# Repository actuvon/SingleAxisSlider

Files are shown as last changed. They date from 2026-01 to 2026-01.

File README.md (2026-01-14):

# Single Axis Slider Project

A simple single-axis CNC motion system for learning about the process of building a custom CNC machine. 

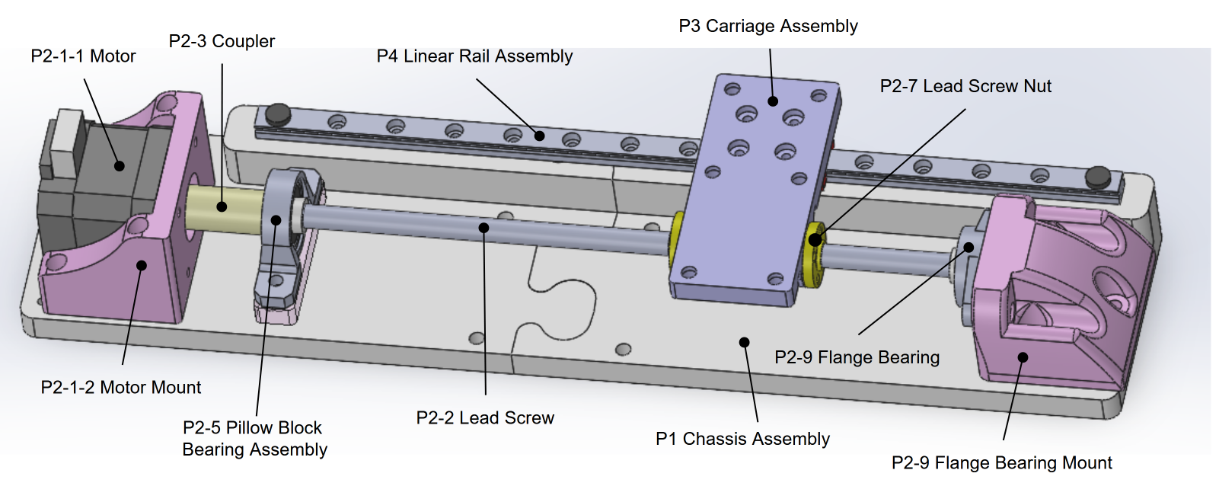
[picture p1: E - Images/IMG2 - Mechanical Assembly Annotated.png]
Mechanical System Diagram D1


## Project objectives (checked when achieved)
- [x] The purpose of this project is to build a cheap motorized linear axis, and to play with different mechanical, electrical, and control options.
- [x] The system should consist of a stepper motor that moves a carriage back and forth along a single axis.
- [x] It should be possible to move the carriage around to specific positions on the axis based on controls from the user.
- [x] A serial/debug interface should be built to let the user try out different settings, or run specific functions on the controller.
- [x] The system should be able to execute standard motion profiles with controlled acceleration and velocity.
- [ ] The controller should be able to run simple g-code programs.
- [ ] The system should include limit switches with auto-homing and collision prevention features.
- [ ] The system should host a web server to lay the groundwork for a user-friendly HMI.
- [ ] The serial/debug interface should be made accessible through the web server via telnet or similar.
- [ ] A web app architecture should be developed to serve an interface to clients which interacts smoothly with the server/controller.
- [ ] A user-friendly HMI should be implemented to jog the motor, home, go to a position, run a g-code command, upload a g-code program, or pause or resume a g-code program that is currently running.
- [ ] The axis should be semi-rigid, so we can pretend that we will use this to mill wood, aluminum, or brass.
- [x] The project should include some basic level of documentation so that readers can get a reasonably good idea of how things work and what's going on.
- [ ] The documentation should be sufficient that someone else could replicate this work, and build the exact same thing.
- [ ] The documentation should be sufficient that a person trying to replicate this work should be able to follow the sequence of decisions that were originally made to build this thing.
- [ ] Use this project as the spindle-carrying X-axis for a full 3-axis CNC mill.

## Files in this repository
Files in this repository are numbered, so that they can be referenced by their document number. Folders in this repository are given letters. Document number 1 in folder C is called document C.1. 
Some folders use part numbers instead of the conventional folder letters. The Part files in folder A and the CAD files in folder B are both examples of this. The CAD folder breaks down it's documents in a slightly different way to keep a clearer revision history.
* **1 - Assembly Definition Document**: This document has the list of parts, and the list of purchase orders and work items that need to be done to build the project. I am working on replacing this Document with MD files such as 3 - Parts.md.
* **3 - Parts.md**: Lists the ID of all parts with a short description and a reference to diagrams that show this part. Includes purchase links and other important details for each part.
* **4 - Ports.md**: TODO: A "Port" is a feature on a part that can be connected to something. It can be a pin/wiring terminal, or it can be a mechanical feature that mates to another mechanical feature on another part. This file details all the ports for each part, which is required to understand document "5 - Connections.md". You often need to look in folder "A - Parts" for a part's "Port Diagram", which shows the name of each port when none is written directly on the part.
* **5 - Connections.md**: TODO: Lists all of the connections between the 'Ports' on various parts. These connections may be made with wires, pipes, fasteners, or others. Notes are given about each connection.
* **6 - TODO.md**: A TODO list to help remind me of the endless pile of tasks yet-to-be-done.
* **Folder A - Parts**: This folder contains detailed information and documents relating to each part. The sub-folders in here are named after the part numbers outlined in document 1 (the assembly definition document). CAD files are not kept in here.
* **Folder B - CAD**: This folder contains all the CAD files, including STL and MDF files used for 3D printing. This is kept seperate from the parts folder to help streamline the CAD modeling workflow. Unfortunately that will make it a bit more of a pain to browse the repository when browsing through parts; you may need to keep one window open for folder A, and another window open for folder B.  Similarly to folder A, all the sub-folders are named after the related part number defined in document 1. I try to keep the STL file for every version of the part that I ever printed, so you can see the progression of changes as I try things and adjust.
* **Folder C - Videos**: As I make YouTube videos to demonstrate different aspects or snapshots of the project, I'll list them here with links and a brief description.
* **Folder D - Diagrams**: All diagrams from document 2 will get exported into here in PDF format. Each diagram will be identified with its diagram number.

## Code
The code that runs on the Arduino Due is kept in the Due's part folder, under **folder A.P5-1.A**. BUT I'll probably move the code over to an entirely different GitHub repo at some point. I'll keep a copy of it here as well though.

I've been uploading this code using PlatformIO, but I think the same code will upload using the Arduino IDE if the main.cpp is renamed to a .ino extension and put in a parent folder with a matching name.

After uploading, I've been accessing the Serial Console using Putty. It should work just fine in the Arduino IDE though. It also works with the PlatformIO terminal.

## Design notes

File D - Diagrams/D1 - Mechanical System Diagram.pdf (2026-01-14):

Rev. 2 - 2026-01-13

A Carriage moves left and right, controlled by a motor that spins a lead screw through a coupler.

The lead screw is supported on one side with a motor, and on the other side with a bearing. The bearing sits on a bearing mount, which bolts to the chassis (shown as ground). On the lead screw rides a carriage assembly. The carriage assembly is driven by two lead screw nuts, which are in turn driven together by the lead screw.

The carriage is supported in linearity and in rotation by the Linear Rail. A Slide is secured to the Linear Rail, and the Carriage is secured to the Slide.

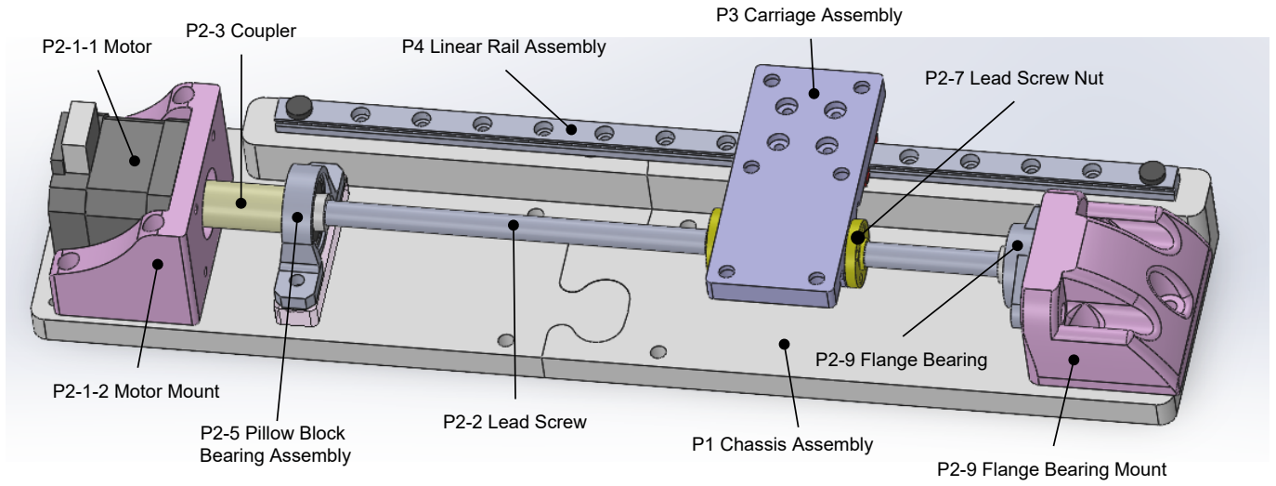
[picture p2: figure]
P1 Chassis Assembly; P2-1-2 Motor Mount; P2-3 Coupler; P2-2 Lead Screw P2-5 Pillow Block; Bearing Assembly; P2-7 Lead Screw Nut; P2-9 Flange Bearing; P2-9 Flange Bearing Mount; P3 Carriage Assembly; P2-1-1 Motor; P4 Linear Rail Assembly

Note: The pillow block bearing was removed from the current version of the assembly because I couldn't get the alignment just right between the linear rail, the flange bearing, the pillow block bearing, and the motor. Failure to align these components perfectly introduces a large amount of friction in the linear rail system. I need to re-develop these parts in a way that makes it possible to align them perfectly.

The ground symbol represents the chassis, which is currently printed in two ABS pieces, joined together. In the future I will want to change this to a single piece of metal, such as a T-rail extrusion.

## D1 - Mechanical System Diagram

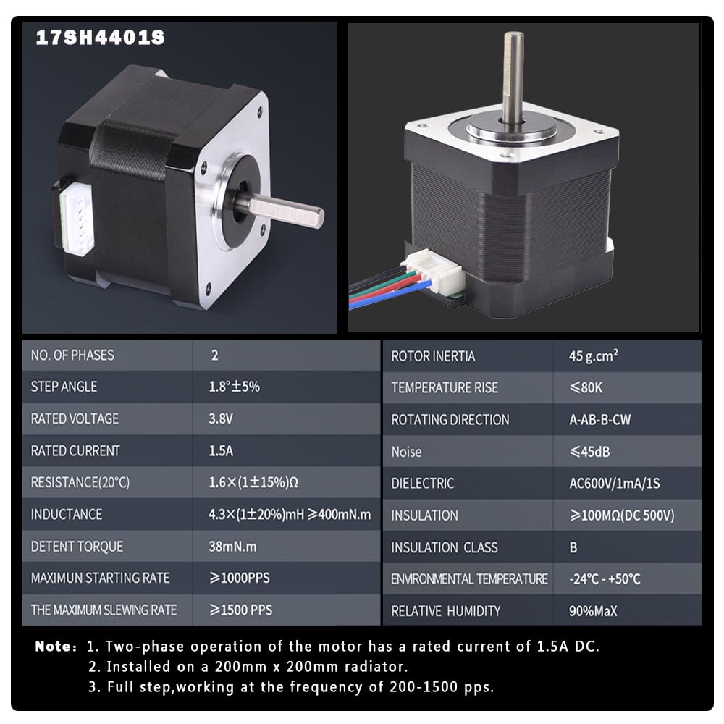
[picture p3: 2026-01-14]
A - Parts/P2-1-1 Stepper Motor/Spec1.jpg

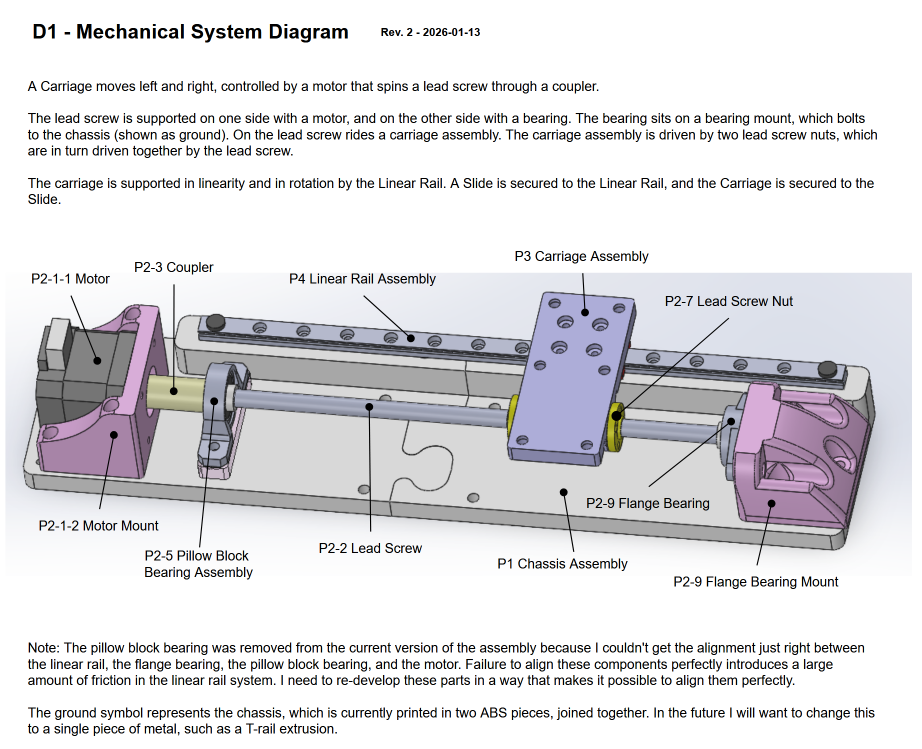
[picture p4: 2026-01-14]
D - Diagrams/D1 - Mechanical System Diagram.png

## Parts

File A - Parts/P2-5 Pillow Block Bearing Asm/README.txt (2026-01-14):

2026-01-13
As of now, this is not in the current version of the build.
The reason is that the alignment wasn't correct enough, so securing this down created too much friction on the lead screw.
When we bring this back, we need to make sure there is enough adjustability to get the alignment perfect.

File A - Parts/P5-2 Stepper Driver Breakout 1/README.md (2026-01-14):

# P5-2 - Stepper Driver Breakout 1

Host board for three DRV8825 stepper driver modules (see part P5-2-2).
Thes boards are capable of microstepping. The breakout board connected the microstep
option pins M0, M1, M2 to !Sleep (called "Wake" here), so the boards are effectively
stuck in 1/32 step mode for maximum microstepping.

Connection numbers start at the red motor power wire and work around counter-clockwise.

Connections
	P5-2:1 	- Motor voltage (red wire). 
			8.2V up to 45V.
			2.5A maximum drive current at 24V and 25°C.

		:2 	- 0V (black wire)
			2.5A maximum drive current.

		:3  - Wake (yellow wire) 

		:4  - Driver 3 !Enable (white wire) (Enable low)
		:5  - Driver 3 Step (blue wire) 
		:6  - Driver 3 Direction (green wire)

		:7	- Driver 2 !Enable (white wire) (Enable low)
		:8  - Driver 2 Step (blue wire)
		:9  - Driver 2 Direction (green wire)

		:10 - Driver 1 !Enable (white wire) (Enable low)
		:11 - Driver 1 Step (blue wire)
		:12 - Driver 1 Direction (green wire)

		:13 - Driver 1 DRIVE B1
		:14 - Driver 1 DRIVE B2
		:15 - Driver 1 DRIVE A1
		:16 - Driver 1 DRIVE A2

		:17 - Driver 2 DRIVE B1
		:18 - Driver 2 DRIVE B2
		:19 - Driver 2 DRIVE A1
		:20 - Driver 2 DRIVE A2

		:21 - Driver 3 DRIVE B1
		:22 - Driver 3 DRIVE B2
		:23 - Driver 3 DRIVE A1
		:24 - Driver 3 DRIVE A2

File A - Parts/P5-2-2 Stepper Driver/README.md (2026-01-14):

#Stepper Driver Breakout 1: Drivers
(parts P-5-2, P-5-3, and P-5-4)

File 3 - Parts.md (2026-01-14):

# Parts

This is a list of all the parts in the system, with brief descriptions.  
To see a **picture/diagram** of the part, check the Diagrams column to see what Diagram(s) it's shown in, then check the related diagram(s) in the **Diagrams folder "D - Diagrams".**  
Details on each part including dimensions, specifications, pinouts, thoughts/plans/problems/rationalle, etc... are given in the **Parts folder "A - Parts".**  
CAD drawings and STL files for 3D Printed parts, or other parts that got modeled for fit are in the **CAD folder "B - CAD".**  
**Purchase links** are provided where possible.  
References to purchase orders (POs), and the PO status are made. These are filled in with MY purchase orders and status; you may wish to clear these columns out and use them for your own build.  
References to Task numbers are made. In the future I want to itemize the tasks needed to perform a build, and create notes/instructions relating to each task.

**Parts in Release #1**

| Part # | Part Name | Part Description | Type | QTY | Connected Parts  | Diagram | PO#  | PO Status | Task # | Task Status | Same as | Purchase Link |
| :--- | :--- | :--- | :--- | :-: | :--- | :--- | :--: | :---: | :----: | :---: | :--- | :---: |
| P1 | Chassis Assembly | The frame that everything else mounts on | Assembly |  1  | P2, P3 | D1 |  x | x | | | | x |
| P1-1 | Chassis Body Print Asm | Both halves of the chassis together | Assembly |  1  | | |  x | x | | | | x |
| P1-1-1 | Chassis Body Print Flange End | The portion of the chassis that the flange bolts to | 3D Print |  1  | | |  x | x | | | | x |
| P1-1-2 | Chassis Body Print Motor End | The portion of the chassis that the motor bolts to | 3D Print |  1  | | |  x | x | | | | x |
| P2 | Drive Assembly | The motor, lead screw, and related supports/power delivery system | Assembly |  1  | | |  x | x | | | | x |
| P2-1 | Motor Assembly | The motor, mount, and related | Assembly |  1  | | D1 |  x | x | | | | x |
| P2-1-1 | Motor | The stepper motor that drives the axis | PO |  1  | P2-1-2 | D1 | PO3  | Received  | x | x | | |
| P2-1-2 | Motor Mount | Mounts the motor to the chassis P1 | 3D Print |  1  | P1, P2-1-1 | D1 |  x | x | | | | |
| P2-1-3 | Motor Mount Screw Asm | Hold the motor to the mount | Assembly |  1  | | |  x | x | | | | x |
| P2-1-3-1 | Motor Mount Screw | | Fastener |  4  | | | | | x | x | | x |
| P2-1-3-2 | Motor Mount Screw Washer | | Fastener |  4  | | | | | x | x | | x |
| P2-2 | Lead Screw | The main transmission element that moves the carriage | PO |  1  | P2-7, P2-7, P2-9 | D1 | PO1  | Received  | x | | | |
| P2-3 | Coupler | Connects the motor shaft to the lead screw | 3D Print |  1  | P2-2 | D1 |  x | x | | | | x |
| P2-7 | Lead Screw Nut | Rides anong the Lead Screw; two are used for anti-backlash adjustment | PO |  2  | | D1 | PO1  | Received  | x | | | |
| P2-9 | Flange Bearing | Holds the end of the Lead Screw opposite the motor | PO |  1  | | D1 | PO8  | Received  | x | | | x |
| P2-10 | Flange Bearing Mount | Holds the flange bearing in place | 3D Print |  1  | | D1 |  x | x | | | | x |
| P3 | Carriage Assembly | | Assembly |  1  | | D1 |  x | x | | | | x |
| P3-1 | Carriage | The main carriage piece | 3D Print |  1  | | |  x | x | | | | x |
| P3-2 | Carriage LeadNut Screws | | Fastener |  8  | | | | | x | | | |
| P3-3 | Carriage LeadNut Screw Nuts | | Fastener |  4  | | | | | x | | | |
| P3-4 | Carriage LeadNut Screw Inserts  | | Fastener |  4  | | | | | x | | | |
| P3-5 | Carriage Slide Screws | | Fastener |  4  | | | | | x | | | |
| P4 | Rail Assembly | | Assembly |  1  | | D1 |  x | x | | | | x |
| P4-1 | Linear Rail | | PO |  1  | | D1 | PO2  | Received  | x | | | |
| P4-2 | Linear Rail Slide | | PO |  1  | | D1 | PO2  | Received  | x | | | |
| P5 | Electronics | | Assembly |  1  | | |  x | x | | | | x |
| P5-1 | Main Controller | Arduino Due | PO |  1  | | | PO10 | Received  | x | | | |
| P5-1-1 | Double-row GPIO Headers Male | | PO |  1  | | | PO5  | Received  | x | | | |
| P5-1-2 | Due Mount | | 3D Print |  1  | | | | | | | | x |
| P5-3 | Independent Stepper Driver 1 | | PO |  1  | | | PO11 | Received  | | | | |
| P5-3-1 | Step Drvr 1 Mount | | 3D Print |  1  | | | | | | | | x |
| P5-3-2 | Step Drvr 1 Mount Clamp | | 3D Print |  2  | | | | | | | | x |
| P5-4 | Control Harness | | Assembly |  1  | | | | | | | | x |
| P5-4-1 | Con: P5-3 Motor side | 8 pin female header | PO |  1  | | | PO12 | Received  | | | | |
| P5-4-2 | Con: P5-3 Ctrl side | 8 pin female header | PO |  1  | | | PO12 | Received  | | | P5-4-1  | |
| P5-4-3 | Due double-row GPIO connector | Dual row female dupont connector | PO |  1  | P5-1-1 | | PO6  | Received  | | | | |
| P5-5 | Brain Mount Plate | Rack plate to host the controller, driver, and connectors | 3D Print |  1  | | | | | | | | x |
| P5-6 | Motor Plug Assembly | | Assembly |  1  | | | | | | | | x |
| P5-6-1 | DB9 Female Connector Asm | | Assembly |  1  | | | | | | | | x |
| P5-6-1-1 | DB9 Female Connector | | PO |  1  | | | | | | | | |
| P5-6-1-2 | DB9 Female Chassis Mount Top | | 3D Print |  1  | | | | | | | | x |
| P5-6-1-3 | DB9 Female Chassis Mount Bottom | | 3D Print |  1  | | | | | | | | x |
| P5-6-1-4 | Female connector mount screws | M5 screws | 3D Print |  2  | | | | | | | | x |
| P5-6-2 | DB9 Male Connector Asm | | Assembly |  1  | | | | | | | | x |
| P5-6-2-1 | DB9 Male Connector | | PO |  1  | | | | | | | | |
| P5-7 | Wires and related | | Misc |  x  | x | x |  x | x | x | x | x | x |
| P5-7-1 | Default hookup wire | 22 AWG stranded silicone-insulated wire kit (multiple colour spools)  | PO | | | | | | | x | | https://www.amazon.ca/dp/B089D29FHC |
| P5-7-2 | Dual DC Power Wire | Dual (Red and Black) 18 AWG silicone-insulated wire spool | PO | | | | | | | x | | https://www.amazon.ca/dp/B07FMRDP87 |
| P5-7-3 | Skinny Hookup Wire | Individual solid-core 28 AWG strands, removed from RJ45 Ethernet wire | PO | | | | | | | x | | https://www.amazon.ca/dp/B0749Y3JTG |
| P6 | Consumables | | Misc |  x  | x | x |  x | x | x | x | x | x |
| P6-1 | ABS Filament | 3D Printer filament used in this project | PO | | | | | | x | x | | |

## Parts not yet added/TODO items

| Part #  | Part Name | Part Description | Type | QTY | Connected Parts | Diagram | PO  | PO Status | Task # | Task Status | Same as | Purchase Link |
| :--- | :--- | :--- | :--- | :-: | :--- | :--- | :-: | :---: | :----: | :---: | :--- | --- |
| P2-11 | Limit Switch A Asm | Not yet implemented | Assembly |  1  | | |  x  | x | | | | |
| P2-11-1 | Limit Switch A | Not yet implemented | PO |  1  | | | PO9 | Planning  | x | | | |
| P2-11-2 | Limit Switch A Mount | Not yet implemented | 3D Print |  1  | | |  x  | x | | | | |
| P2-12 | Limit Switch B Asm | Not yet implemented | Assembly |  1  | | |  x  | x | | | | |
| P2-12-1 | Limit Switch B | Not yet implemented | PO |  1  | | | PO9 | Planning  | x | | | |
| P2-12-2 | Limit Switch B Mount | Not yet implemented | 3D Print |  1  | | |  x  | x | | | | |
| | Rack System | Electronic controls get mounted on plates that get installed in the rack system | Assembly |  1  | | |  x  | x | | | | |

## Inactive/archived parts NOT in above release

| Part # | Part Name | Part Description | Type | QTY | Connected Parts | Diagram | PO  | PO Status | Task # | Task Status | Same as | Purchase Link | Why inactive |
| :--- | :--- | :--- | :--- | :-: | :--- | :--- | :-: | :---: | :----: | :---: | :--- | --- | --- |
| P2-1-4 | Motor Mount Chassis Screw Asm | Hold the mount to the base | Assembly |  4  | | |  x  | x | | | | | Holes don't lign up with chassis |
| P2-1-4-1 | Motor Mount Chassis Screw | | Fastener |  4  | | | | | x | | | | Bad parent really, it's the chassis's fault  |
| P2-1-4-2 | Motor Mount Chassis Screw Nut | | Fastener |  4  | | | | | x | | | | Bad parent really, it's the chassis's fault  |
| P2-3-1 | Coupler Motor Set Screw | | Fastener |  1  | | | | | x | | | | To be added later / Not needed at low torque |
| P2-3-2 | Coupler Leadscrew Set Screw | | Fastener |  1  | | | | | x | | | | To be added later / Not needed at low torque |
| P2-5 | Pillow Block Bearing Assembly | Not in current version - see note in part file | Assembly |  1  | | D1 |  x  | x | | | | | Bad design, causes too much friction |
| P2-5-1 | Pillow Block Bearing | K08 Pillow Block Bearing | PO |  1  | | | PO7 | Received  | x | | | | Bad parent |
| P2-5-2 | Pillow Block Bearing Mount | | 3D Print |  1  | | |  x  | x | | | | | Bad parent |
| P2-5-3 | Pillow Block Mounting Screws  | | Fastener |  2  | | | | | x | | | | Bad parent |
| P5-2 | Stepper Driver Breakout 1 | Perf Board (original design) | Assembly | | | | | | | | | | Replaced with superior part |
| P5-2-1 | SDB1: Perf Board | Board with connections and wires | PO | | | | | | | | | | Bad parent |
| P5-2-2 | SDB1: Driver 1 | Leftmost driver viewed from motor side | PO | | | | | | | | P5-2-1  | | Bad parent |
| P5-2-3 | SDB1: Driver 2 | Middle driver | PO | | | | | | | | P5-2-1  | | Bad parent |
| P5-2-4 | SDB1: Driver 3 | Rightmost driver viewed from motor side | PO | | | | | | | | P5-2-1  | | Bad parent |

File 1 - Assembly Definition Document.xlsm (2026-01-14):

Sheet: Overview
Overview
This document pertains to the single axis slider project. See the README.md.
See document 2 - Single Axis Slider Diagrams
This document relates to build version v0

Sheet: Parts
Systems are made of parts. There are a few main subassemblies in the system.
Each subassembly gets a part number. Some parts of subassemblies come from purchase orders (buying things) and some parts of subassemblies come from work orders (doing things).
Some parts of subassemblies are subassemblies.
In this table we itemise all subassemblies and parts, give them unique numbers, and indicate what diagrams they can be found in and what other parts they connect to.
On the far right, we also link the related purchase orders and work orders, and link in their status so we can monitor our progress as we do a build.
Parts
 |  |  |  |  |  |  |  | Construction Progress
Part # | Part Name | Part Description | Type | Active | QTY | Connected Parts | Diagram | PO | PO Status | Task # | Task Status | Same as
P1 | Chassis Assembly | The frame that everything else mounts on. | Assembly | 1 | 1 | P2, P3 | D1 | x | x
P1-1 | Chassis Body Print Asm | Both halves together | Assembly | 1 | 1 |  |  | x | x
P1-1-1 | Chassis Body Print Flange End |  | 3D Print | 1 | 1 |  |  | x | x
P1-1-2 | Chassis Body Print Motor End |  | 3D Print | 1 | 1 |  |  | x | x
P2 | Drive Assembly |  | Assembly | 1 | 1 |  |  | x | x
P2-1 | Motor Assembly |  | Assembly | 1 | 1 |  |  | x | x
P2-1-1 | Motor | Bipolar stepper motor | PO | 1 | 1 |  |  | PO3 | Received | x | x
P2-1-2 | Motor Mount |  | 3D Print | 1 | 1 |  |  | x | x
P2-1-3 | Motor Mount Screw Asm | Hold the motor to the mount | Assembly | 1 | 1 |  |  | x | x
P2-1-3-1 | Motor Mount Screw |  | Fastener | 1 | 4
P2-1-3-2 | Motor Mount Screw Washer |  | Fastener | 1 | 4
P2-1-4 | Motor Mount Chassis Screw Asm | Hold the mount to the base | Assembly | 1 | 4 |  |  | x | x
P2-1-4-1 | Motor Mount Chassis Screw |  | Fastener | 1 | 4
P2-1-4-2 | Motor Mount Chassis Screw Nut |  | Fastener | 1 | 4
P2-2 | Lead Screw | T8 lead screw | PO | 1 | 1 |  |  | PO1 | Received
P2-3 | Coupler |  | 3D Print | 1 | 1 |  |  | x | x
P2-3-1 | Coupler Motor Set Screw |  | Fastener | 0 | 1
P2-3-2 | Coupler Leadscrew Set Screw |  | Fastener | 0 | 1
P2-5 | Pillow Block Bearing Assembly |  | Assembly | 0 | 1 |  |  | x | x
P2-5-1 | Pillow Block Bearing | K08 Pillow Block Bearing | PO | 0 | 1 |  |  | PO7 | Received
P2-5-2 | Pillow Block Bearing Mount |  | 3D Print | 0 | 1 |  |  | x | x
P2-5-3 | Pillow Block Mounting Screws |  | Fastener | 0 | 2
P2-7 | Lead Screw Nut | T8 lead screw nuts (2 needed) | PO | 1 | 2 |  |  | PO1 | Received
P2-9 | Flange Bearing | K08 Flange bearing | PO | 1 | 1 |  |  | PO8 | Received
P2-10 | Flange Bearing Mount |  | 3D Print | 1 | 1 |  |  | x | x
P2-11 | Limit Switch A Asm |  | Assembly | 1 | 1 |  |  | x | x
P2-11-1 | Limit Switch A |  | PO | 1 | 1 |  |  | PO9 | Planning
P2-11-2 | Limit Switch A Mount |  | 3D Print | 1 | 1 |  |  | x | x
P2-12 | Limit Switch B Asm |  | Assembly | 1 | 1 |  |  | x | x
P2-12-1 | Limit Switch B |  | PO | 1 | 1 |  |  | PO9 | Planning
P2-12-2 | Limit Switch B Mount |  | 3D Print | 1 | 1 |  |  | x | x
P3 | Carriage Assembly |  | Assembly | 1 | 1 |  |  | x | x
P3-1 | Carriage | The main carriage piece | 3D Print | 1 | 1 |  |  | x | x
P3-2 | Carriage LeadNut Screws |  | Fastener | 1 | 8
P3-3 | Carriage LeadNut Screw Nuts |  | Fastener | 1 | 4
P3-4 | Carriage LeadNut Screw Inserts |  | Fastener | 1 | 4
P3-5 | Carriage Slide Screws |  | Fastener | 1 | 4
P4 | Rail Assembly |  | Assembly | 1 | 1 |  |  | x | x
P4-1 | Linear Rail |  | PO | 1 | 1 |  |  | PO2 | Received
P4-2 | Linear Rail Slide |  | PO | 1 | 1 |  |  | PO2 | Received
P5 | Electronics |  | Assembly | 1 | 1 |  |  | x | x
P5-1 | Main Controller | Arduino Due | PO | 1 | 1 |  |  | PO10 | Received
P5-1-1 | Double-row GPIO Headers Male |  | PO | 1 | 1 |  |  | PO5 | Paid
P5-1-2 | Due Mount |  | 3D Print | 1 | 1
P5-2 | Stepper Driver Breakout 1 | Perf Board (original design) | Assembly | 0
P5-2-1 | SDB1: Perf Board | Board with connections and wires |  | 0
P5-2-2 | SDB1: Driver 1 | Leftmost driver viewed from motor side |  | 0
P5-2-3 | SDB1: Driver 2 | Middle driver |  | 0
P5-2-4 | SDB1: Driver 3 | Rightmost driver viewed from motor side |  | 0
P5-2:1 | SDB1: Motor voltage | Red wire |  | 0
P5-2:2 | SDB1: 0V | Black wire |  | 0
P5-2:3 | SDB1: Wake | Yellow wire |  | 0
P5-3 | Independent Stepper Driver 1 |  | PO | 1 | 1 |  |  | PO11 | Received
P5-3-1 | Step Drvr 1 Mount |  | 3D Print | 1 | 1
P5-3-2 | Step Drvr 1 Mount Clamp |  | 3D Print | 1 | 2
P5-4 | Control Harness |  | Assembly | 1 | 1
P5-4-1 | Con: P5-3 Motor side | 8 pin female header | PO | 1 | 1 |  |  | PO12 | Received
P5-4-2 | Con: P5-3 Ctrl side | 8 pin female header | PO | 1 | 1 |  |  | PO12 | Received |  |  | P5-4-1
P5-4-3 | Due double-row GPIO connector | Dual row female dupont connector | PO | 1 | 1 | P5-1-1 |  | PO6 | Paid
P5-5 | Brain Mount Plate | Rack plate to host the controller, driver, and connectors | 3D Print | 1 | 1
P5-6 | Motor Plug Assembly |  | Assembly | 1 | 1
P5-6-1 | DB9 Female Connector Asm |  | Assembly | 1 | 1
P5-6-1-1 | DB9 Female Connector |  | PO | 1 | 1
P5-6-1-2 | DB9 Female Chassis Mount Top |  | 3D Print | 1 | 1
P5-6-1-3 | DB9 Female Chassis Mount Bottom |  | 3D Print | 1 | 1
P5-6-1-4 | Female connector mount screws | M5 screws | 3D Print | 1 | 2
P5-6-2 | DB9 Male Connector Asm |  | Assembly | 1 | 1
P5-6-2-1 | DB9 Male Connector |  | PO | 1 | 1
P6 | Rack System | Electronic controls get mounted on plates that get installed in the rack system | Assembly | 1 | 1

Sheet: POs
This page lists the different purchases that need to be made to build the project. |  |  |  |  |  |  | Statuses:
The line items within each purchase are described in the Order Details sheet. |  |  |  |  |  |  | Planning
Most Order Detail lines should reference parts, but some order lines relate to services instead. |  |  |  |  |  |  | RFQ Submitted
This sheet is about checking what things have or haven't been ordered, and making sure they arrive on time. |  |  |  |  |  |  | Quoted
 |  |  |  |  |  |  | Sent to Accounting
 |  |  |  |  |  |  | Paid
 |  |  |  |  |  |  | Receiving
 |  |  |  |  |  |  | Received
Purchase Orders |  |  | Total : | $364.15 | (CAD)
 |  |  |  |  |  |  |  |  | Purchasing Documents
Order # | Name | Description | Vendor | Amount (CAD) | Included/Cancelled | Status | Last Updated | Last Note | SO# | PO# | QT# | IN#
PO1 | T8 lead screws | QTY 2. The main lead screw for the axis-drive. | Amazon | $54.29 | Included | Received | 2025-11-03 | Order Received
PO2 | Linear Rails | Main linearity provider. | Amazon | $20.14 | Included | Received | 2025-10-31 | Order Received
PO3 | Motors | Two Stepper motors | Amazon | $20.15 | Included | Received | 2025-11-05 | Order Received
PO4 | M3 inserts | 100 inserts | Amazon | $12.31 | Included | Paid | 2025-11-24 | Order placed
PO5 | Due Headers M | Dual row male duponts for the Due | Amazon | $23.40 | Included | Paid | 2025-11-24 | Order placed
PO6 | Due Connectors F | Dual row female duponts for the Due | Amazon | $19.48 | Included | Paid | 2025-11-24 | Order placed
PO7 | Pillow Block Bearings | 4 pillow block bearings | Amazon | $14.55 | Cancelled | Received
PO8 | Flange Bearings | 4 flange bearings | Amazon | $17.80 | Included | Received
PO9 | Limit Switches |  | Amazon | $13.44 | Included | Planning
PO10 | Arduino Due |  | Amazon | $67.20 | Included | Received | 2024-01-01 | I've had this thing for ages, actually
PO11 | DRV8825 Drivers | 6 drivers | Amazon | $24.63 | Included | Received | 2024-07-22 | 0
PO12 | Dupont headers | male and female, 10 pcs each x 40 pins | Amazon | $17.91 | Included | Received | 2025-11-24 | 0
PO14 | TMC2209 drivers | 6 drivers | Amazon | $43.19 | Included | Received | 2026-01-12 | Planned upgrade
PO15 | DB9 connectors | 10 pairs including the M and F sides | Amazon | $15.67 | Included | Received | 2024-01-01 | I've had these for ages

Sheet: PODs
Orders often have a number of different line items on the receipt.
Thacking those is important. We need to check the lines against the parts that we need to verify that they are correct,
to verify that everything gets purchased on time,and to verify things get purchased in the correct style and quantity.
Sometimes a single order line might apply to multiple parts. When this happens, make one order detail row for each [part#, orderline#] combination
Purchase Order Details
 |  |  |  |  |  |  |  |  |  |  |  |  |  | ($CAD)
POD# | PO # | Order Name | Line Num. | Order Line Name | Part # | Part Name | Part Desc | Part Ordering Req. | Part Qty | Status | Vendor | SKU | Link | Price/ea | Order Qty | Subtotal (CAD) | Notes
PO1.1 | PO1 | T8 lead screws | 1 | 2PCS 250mm（9.84 Inches）Tr8x8 Lead Screw with T8 Brass Nut (Acme Thread, 2mm Pitch, 4 Starts, 8mm Lead) for LCD DLP SLA 3D Printer Z Axis and CNC Machine | P2-2 | Lead Screw | T8 lead screw |  | 2 | Received | Amazon | B0B8RKN89V | https://www.amazon.ca/dp/B0B8RKN89V | 25.63 | 1 | 25.63
PO1.1 | PO1 | T8 lead screws | 1 | 2PCS 250mm（9.84 Inches）Tr8x8 Lead Screw with T8 Brass Nut (Acme Thread, 2mm Pitch, 4 Starts, 8mm Lead) for LCD DLP SLA 3D Printer Z Axis and CNC Machine | P2-7 | Lead Screw Nut | T8 lead screw nuts (2 needed) |  | 2 | Received | Amazon | B0B8RKN89V | https://www.amazon.ca/dp/B0B8RKN89V | 0 | 0 | 0 | Included with the leadscrew
PO10.1 | PO10 | Arduino Due | 1 |  | P5-1-1 | Double-row GPIO Headers Male | 0 |  | 1 | Received | Amazon |  | https://www.amazon.ca/Arduino-A000062-Due/dp/B00A6C3JN2 |  |  | 0
PO10. | PO10 | Arduino Due |  |  |  | 0 | 0 |  |  | Received | Amazon |  | https://www.amazon.ca/Arduino-A000062-Due/dp/B00A6C3JN2 |  |  | 0
PO11. | PO11 | DRV8825 Drivers |  |  |  | 0 | 0 |  |  | Received | Amazon |  | https://www.amazon.ca/dp/B0BLKPQ5NY |  |  | 0
PO12. | PO12 | Dupont headers |  |  |  | 0 | 0 |  |  | Received | Amazon |  | https://www.amazon.ca/dp/B08CMNRXJ1 |  |  | 0
PO14. | PO14 | TMC2209 drivers |  |  |  | 0 | 0 |  |  | Received | Amazon |  | https://www.amazon.ca/dp/B08WZFK9KT |  |  | 0
PO15. | PO15 | DB9 connectors |  |  |  | 0 | 0 |  |  | Received | Amazon |  | https://www.amazon.ca/dp/B07C6W5TJ9 |  |  | 0
PO2.1 | PO2 | Linear Rails | 1 |  |  | 0 | 0 |  | 1 | Received | Amazon |  | https://www.amazon.ca/dp/B0BYZ5NDJ2 |  |  | 0
PO3.1 | PO3 | Motors | 1 | Nema17 Stepper Motor – High Torque 4-Lead Motor with 1m Cable, Ideal for CNC, XYZ 3D Printing – Efficient and Versatile 3D Printer Motors (Pack of 2pcs) | P2-1-1 | Motor | Bipolar stepper motor | 1.5A NEMA17 | 2 | Received | Amazon | B0D1VJ9HHY | https://www.amazon.ca/dp/B0D1VJ9HHY | 20.15 | 1 | 20.15 | Connectors included
PO4.1 | PO4 | M3 inserts | 1 | HANGLIFE Heat-Set Threaded Inserts, M3 Heat Set Insert for 3D Printing Components and Plastic Parts - Brass Metric Knurled Nuts (100 Pieces) | x | ? | ? |  | 100 | Paid | Amazon |  | https://www.amazon.ca/dp/B0CS6VZYL8 | 10.99 | 1 | 10.99
PO5.1 | PO5 | Due Headers M | 1 | uxcell 25Pcs 2.54mm Pitch Dual Row 80-Pin Male 90 Degree Pin Header Connector | P5-1-1 | Double-row GPIO Headers Male | 0 |  | 25 | Paid | Amazon |  | https://www.amazon.ca/dp/B00REGUVCA | 20.89 | 1 | 20.89
PO6.1 | PO6 | Due Connectors F | 1 |  | P5-4-1 | Con: P5-3 Motor side | 8 pin female header |  | 20 | Paid | Amazon |  | https://www.amazon.ca/dp/B0BZPN6CMX | 19.48 | 1 | 19.48
PO7. | PO7 | Pillow Block Bearings |  |  |  | 0 | 0 |  |  | Received | Amazon |  | https://www.amazon.ca/dp/B07SWX3P6T |  |  | 0
PO8. | PO8 | Flange Bearings |  |  |  | 0 | 0 |  |  | Received | Amazon |  | https://www.amazon.ca/dp/B0BW6QTRRX |  |  | 0
PO9. | PO9 | Limit Switches |  |  |  | 0 | 0 |  |  | Planning | Amazon |  | https://www.amazon.ca/dp/B07T9DWV4J |  |  | 0

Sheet: PO Hist.
WARNING: double clicking a cell in the Date column will set it to today's date.
Keep track of the order as updates come in. When something happens to an order's status (say, we get confirmation that it was shipped),
put the update in here. Just enter the PO number, the date, and the current status of the order, then a note about what happened.
The latest update for any order in this table will show up in the POs sheet.
Purchase Order History
PO | Date | Status | PO Name | Note
PO1 | 2025-11-03 | Received | T8 lead screws | Order Received
PO2 | 2025-10-31 | Received | Linear Rails | Order Received
PO3 | 2025-11-05 | Received | Motors | Order Received
PO4 | 2025-11-24 | Paid | M3 inserts | Order placed
PO5 | 2025-11-24 | Paid | Due Headers M | Order placed
PO6 | 2025-11-24 | Paid | Due Connectors F | Order placed
PO9 | 2026-01-13 | Planning | Limit Switches | Planning
PO7 | 2025-11-08 | Received | Pillow Block Bearings
PO8 | 2025-11-08 | Received | Flange Bearings
PO10 | 2024-01-01 | Received | Arduino Due | I've had this thing for ages, actually
PO11 | 2024-07-22 | Received | DRV8825 Drivers
PO12 | 2025-11-24 | Received | Dupont headers
PO14 | 2026-01-12 | Received | TMC2209 drivers | Planned upgrade
PO15 | 2024-01-01 | Received | DB9 connectors | I've had these for ages

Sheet: Tasks
Projects involve a number of tasks that need to be completed. |  |  | Priorities: | Statuses:
This sheet lets us list the tasks we need to do, and monitor the status of each task. |  |  | Highest | Planning
This sheet pairs with the task history sheet "T Hist." |  |  | High | Started (Active)
 |  |  | Average | On Hold
 |  |  | Low | Completed
 |  |  | Lowest
 |  |  | Completed
Tasks
Task # | Name | Description | Priority | Status | Last Updated | Last Note
T1 | Outline objectives |  | Completed | Completed | 2025-10-01 | Identified in the README.md
T2 | Begin identifying key parts |  | Completed | Completed | 2025-10-01 | Outlined in diagram D1 and included in the Parts sheet
T3 | First concept diagram |  | Completed | Completed | 2025-10-01 | Generated diagram D1
T4 | Stepper Driver Mounts | CAD the new mount for the stepper driver boards - with clips for the female dupont harness connectors. | Highest | Completed | 2025-12-01 | Finished some time in december
T5 | Due Lateral Headers | Desolder all the pin headers like a fucking masochist, then put right angle headers on instead. | High | Completed | 2025-12-01 | Finished some time in december
T6 | Document past orders | Get all past orders in this spreadsheet | Average | Completed | 2026-01-13 | Just did this

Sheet: T Hist.
WARNING: double clicking a cell in the Date column will set it to today's date.
Keep track of tasks progress gets updated. When something happens to a task's status (say, we do a bunch of work on a part),
put the update in here. Just enter the task number, the date, and a note about what happened.
The latest update for any task in this table will show up in the Tasks sheet.
Task History
Task | Date | Status | Task Name | Note
T1 | 2025-10-01 | Completed | Outline objectives | Identified in the README.md
T2 | 2025-10-01 | Completed | Begin identifying key parts | Outlined in diagram D1 and included in the Parts sheet
T3 | 2025-10-01 | Completed | First concept diagram | Generated diagram D1
T4 | 2025-11-25 | Planning | Stepper Driver Mounts | I just came up with the plan to have lateral male dupont pin rows as the standard connector for module boards, with female dupont rows connecting to them, and the master harness getting wired in to that. This is a new sort of idea and a big change from the old plan, but I think I like it. Let's get the mechanical part of the mount down for the little stepper driver boards first. We need to have a 3D printed base with clips to secure the female dupont rows in place when they're plugged in. For now, those clips that go on the female dupont harness connectors will be the main thing holding the stepper driver board in place. Later, I might come up with something to secure the board inself even when it isn't plugged in to anything.
T5 | 2025-11-25 | Planning | Due Lateral Headers | De-solder all the headers so you can put lateral ones on. You fucking monster why did you decide this was necessary.
T6 | 2025-11-25 | Started (Active) | Document past orders | There are Amazon orders and perhaps other orders that were done before this spreadsheet was a thing. Get that shit in here.
T4 | 2025-12-01 | Completed | Stepper Driver Mounts | Finished some time in december
T5 | 2025-12-01 | Completed | Due Lateral Headers | Finished some time in december
T6 | 2026-01-13 | Completed | Document past orders | Just did this

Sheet: Project Journal
WARNING: double clicking a cell in the Date column will set it to today's date.
Take Notes on what was done at different points in time.
Task History
Date | Note
2026-01-13 | JOURNAL SHEET CREATED The first project overview video was posted a few days ago. I am getting the documentation together to get it ready for the initial post to GitHub. I think that all of the purchasing related to this project is accounted for, although I have not listed the tools I used or the cost of the 3d printing filament. The parts are listed with a basic diagram though, and the code is included. I think we're almost ready to post.

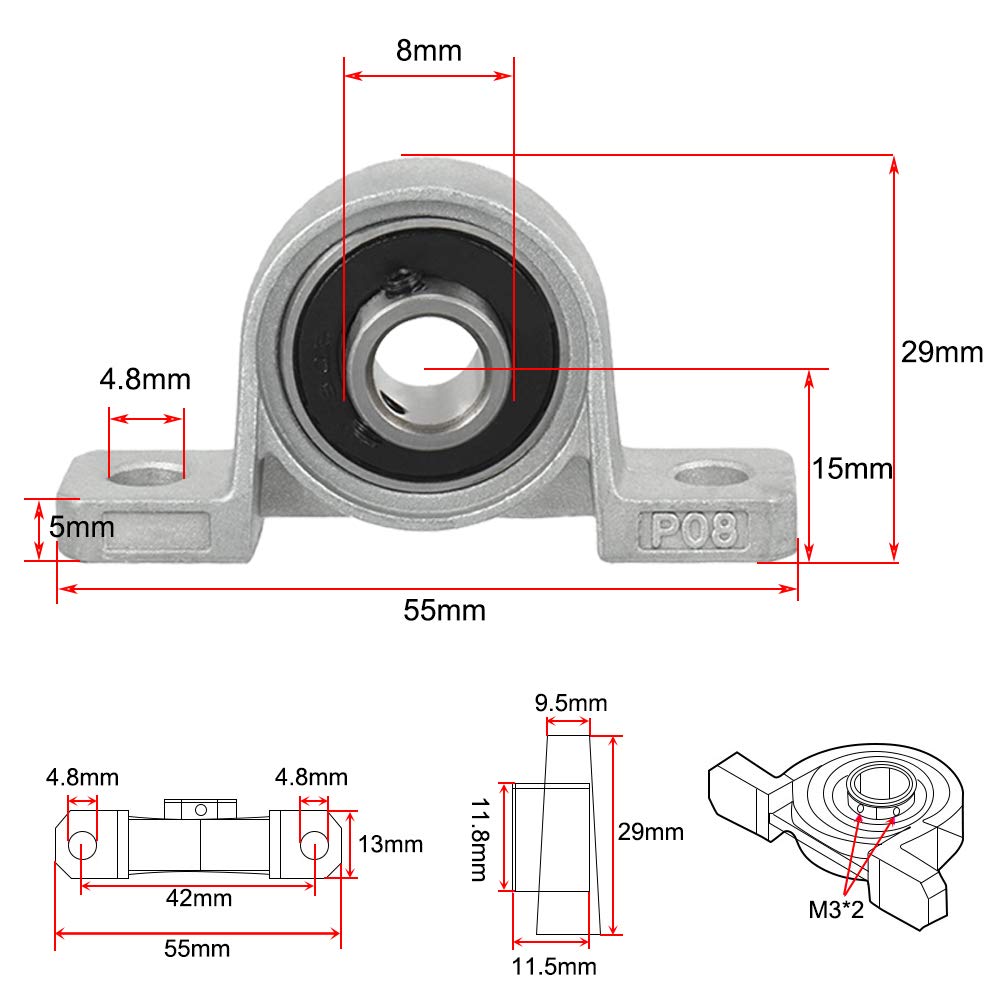
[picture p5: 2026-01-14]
A - Parts/P2-5-1 Pillow Block Bearing/P2-5-1 Pillow Block Bearing.jpg

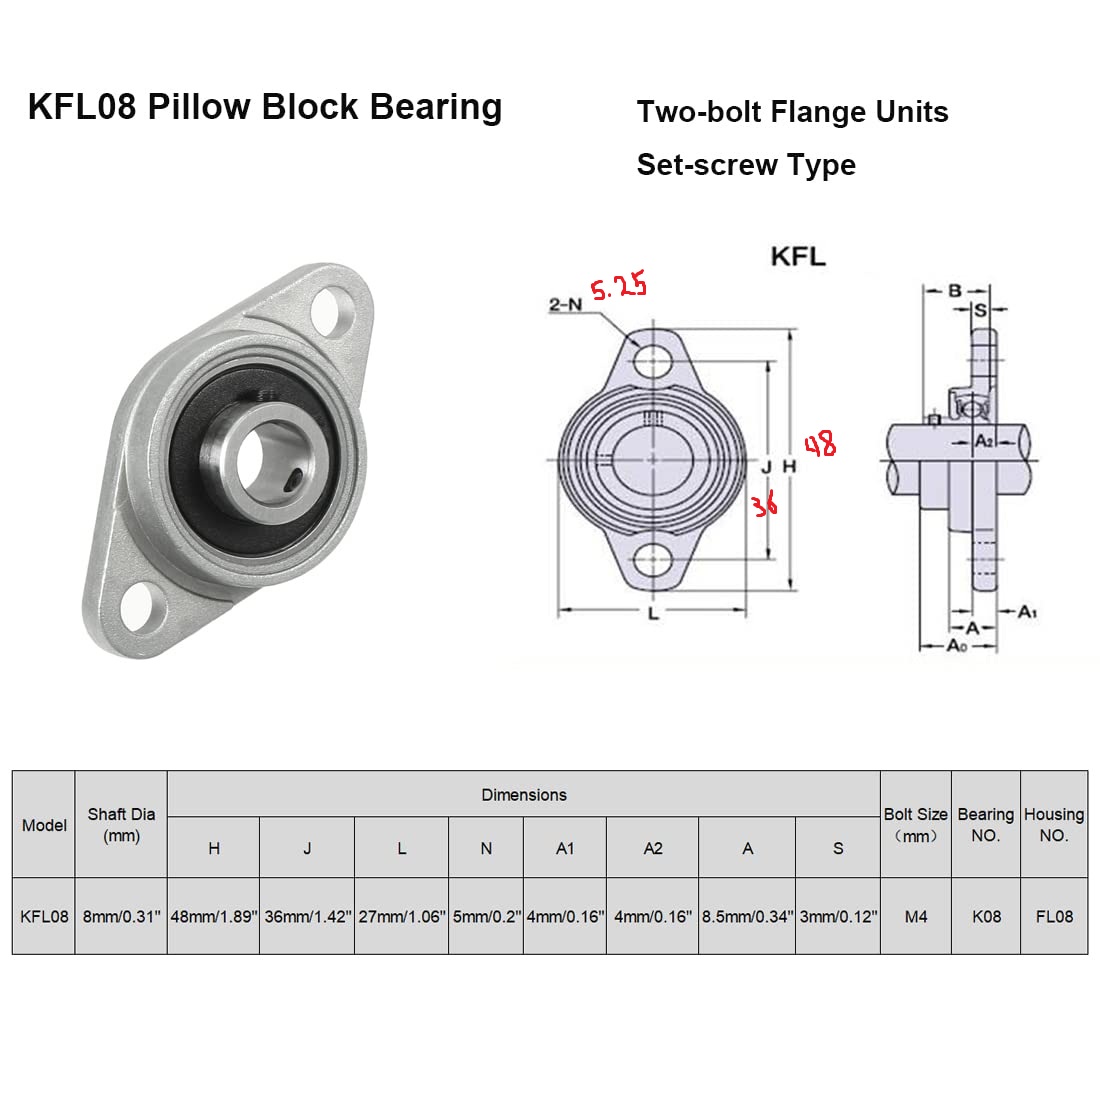
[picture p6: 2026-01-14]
A - Parts/P2-9 Flange Bearing/P2-9 Flange Bearing.jpg

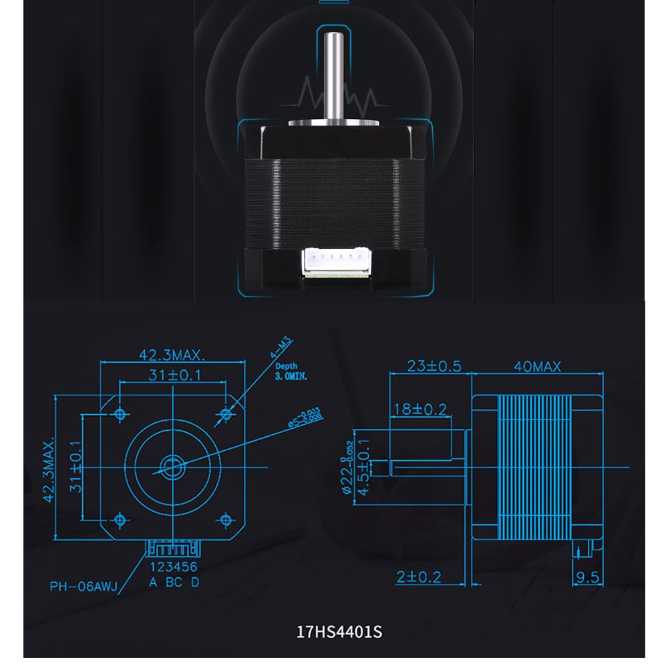
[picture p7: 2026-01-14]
A - Parts/P2-1-1 Stepper Motor/Dimensions.jpg

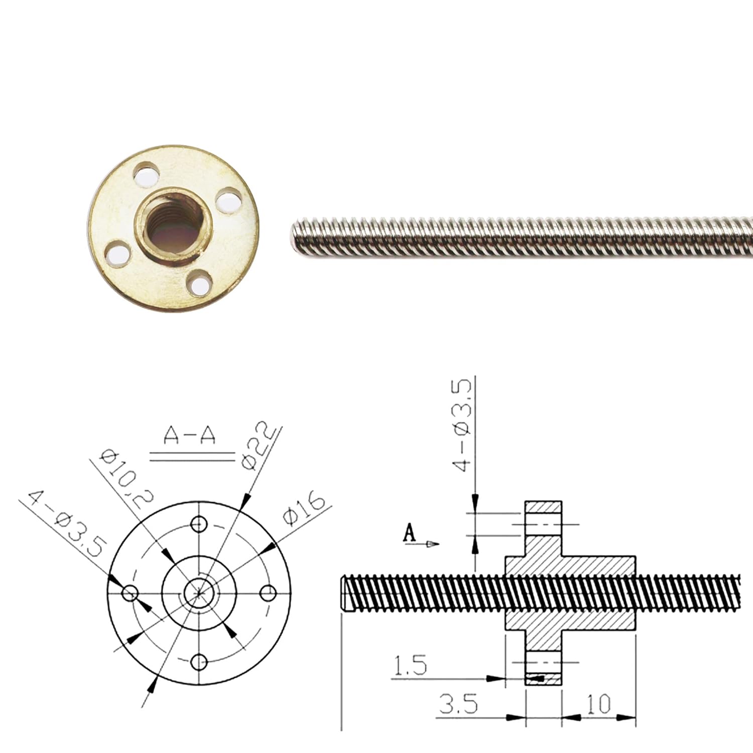
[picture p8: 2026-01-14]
A - Parts/P2-2 Lead Screw/P2-2 Lead Screw.jpg

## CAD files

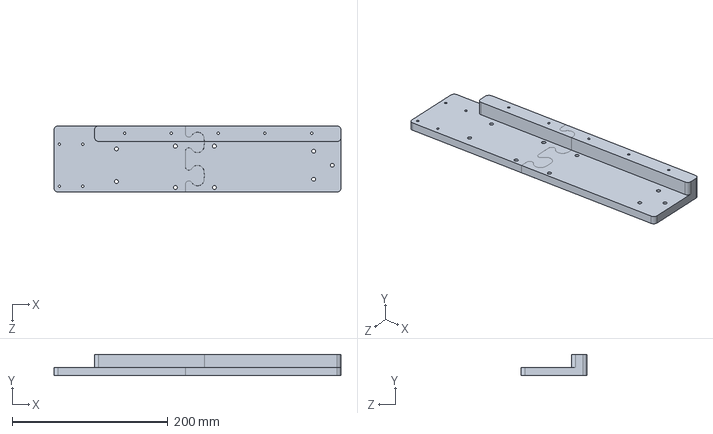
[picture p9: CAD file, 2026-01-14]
B - CAD/P1-1 Chassis Body Print Asm/2025-11-10 - 855 - v0/P1-1 Chassis Body Print Asm.SLDPRT
368.0 x 27.0 x 85.0 mm

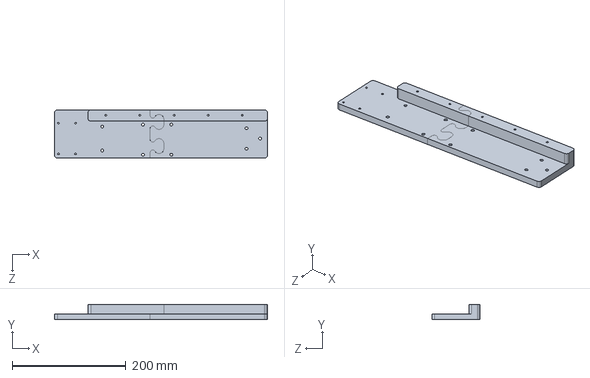
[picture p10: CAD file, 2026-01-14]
B - CAD/P1-1 Chassis Body Print Asm/P1-1 Chassis Body Print Asm.SLDPRT
375.0 x 27.0 x 85.0 mm

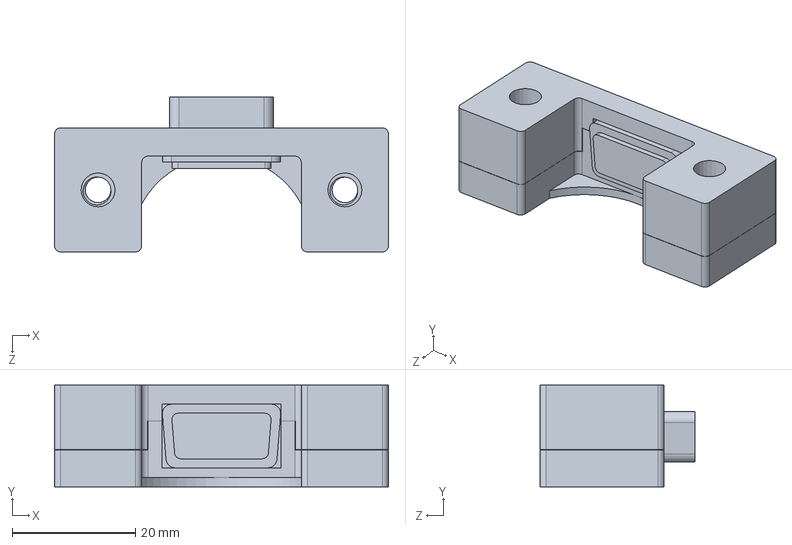
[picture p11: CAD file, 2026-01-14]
B - CAD/P5-6-3 DB9/DB9 Chassis Mount Asm.SLDPRT
54.1 x 16.5 x 25.1 mm

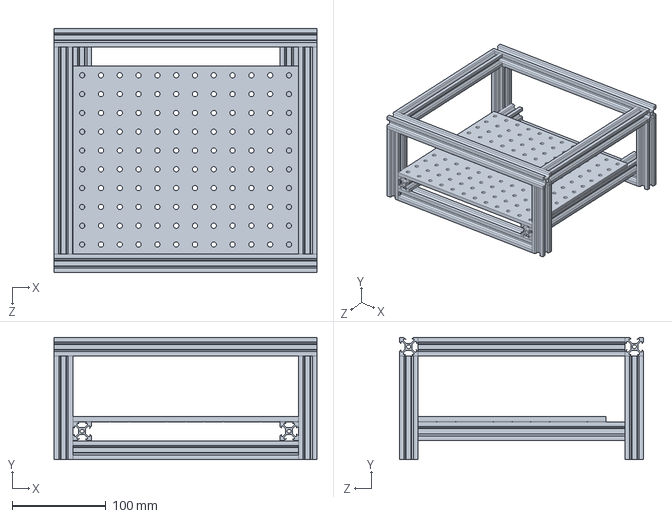
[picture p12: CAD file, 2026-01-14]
B - CAD/P6 Rack System/RackAsm.SLDPRT
279.8 x 129.8 x 260.0 mm

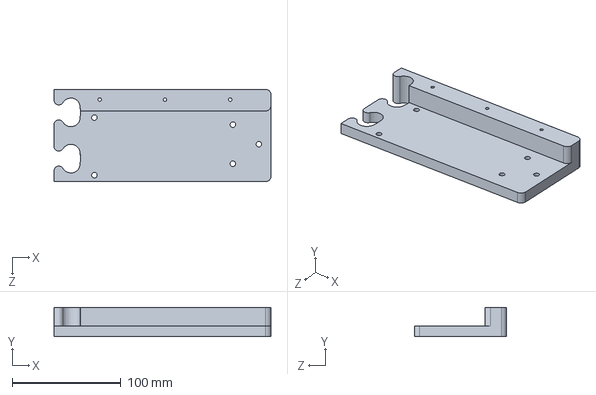
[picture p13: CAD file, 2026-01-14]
B - CAD/P1-1-1 Chassis Body Print Flange End/P1-1-1 Chassis Body Print Flange End.SLDPRT
199.5 x 27.0 x 85.0 mm

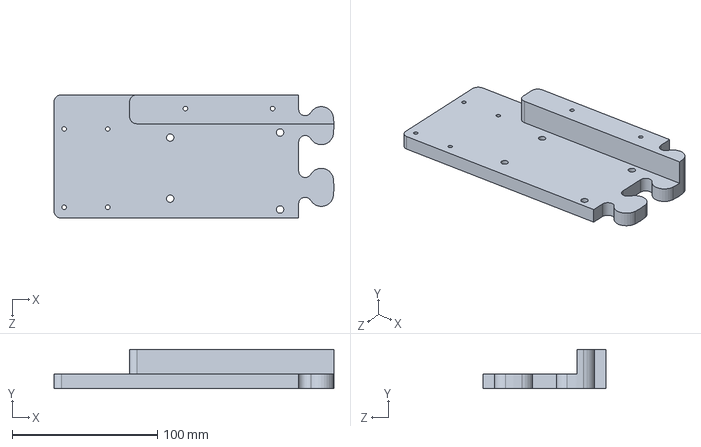
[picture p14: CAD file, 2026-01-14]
B - CAD/P1-1-2 Chassis Body Print Motor End/P1-1-2 Chassis Body Print Motor End.SLDPRT
192.8 x 27.0 x 85.0 mm

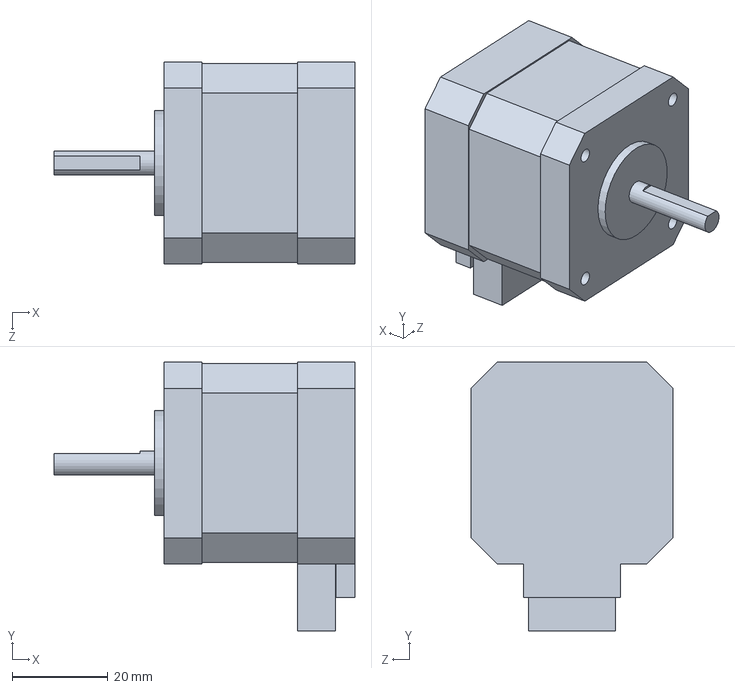
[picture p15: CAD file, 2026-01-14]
B - CAD/P2-1-1 Motor/P2-1-1 Motor.SLDPRT
63.0 x 56.3 x 42.3 mm

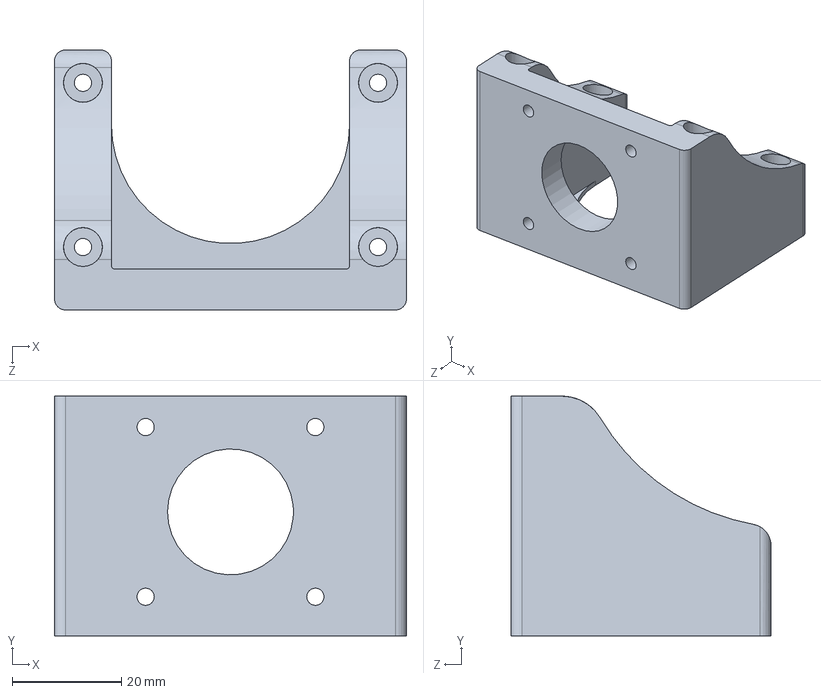
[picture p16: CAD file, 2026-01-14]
B - CAD/P2-1-2 MotorMount/P2-1-2 MotorMount.SLDPRT
64.3 x 43.8 x 47.5 mm

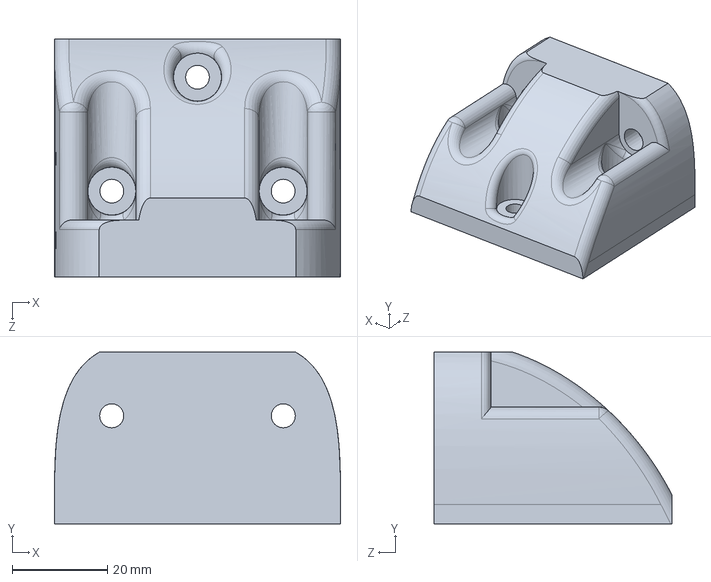
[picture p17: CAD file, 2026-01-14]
B - CAD/P2-10 Flange Bearing Mount/Flange Bearing Mount - 2025-11-09 - 2117.SLDPRT
60.0 x 36.0 x 50.0 mm

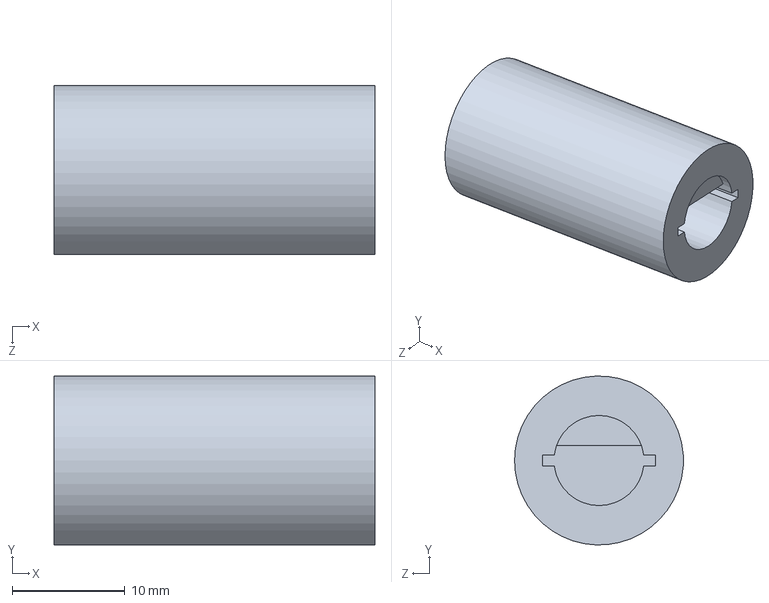
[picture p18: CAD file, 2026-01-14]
B - CAD/P2-3 Coupler/P2-3 Coupler.SLDPRT
28.5 x 15.0 x 15.0 mm

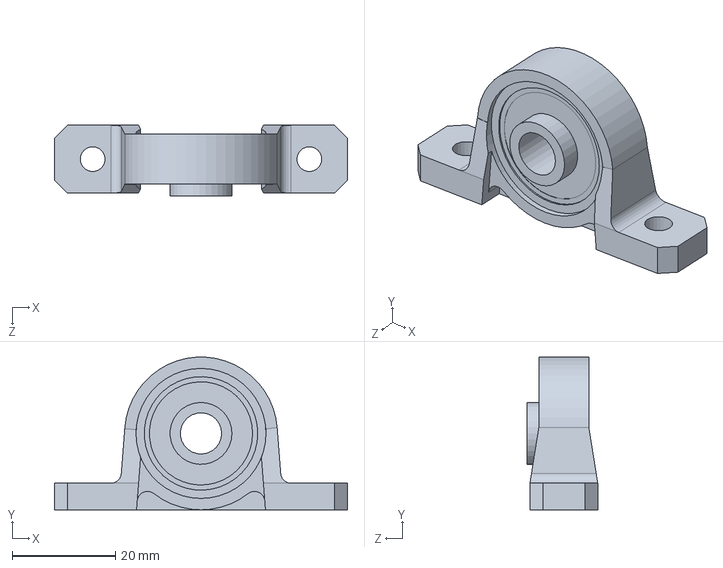
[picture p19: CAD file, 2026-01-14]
B - CAD/P2-5-1 Pillow Block Bearing/P2-5-1 Pillow Block Bearing.SLDPRT
56.8 x 29.6 x 13.7 mm

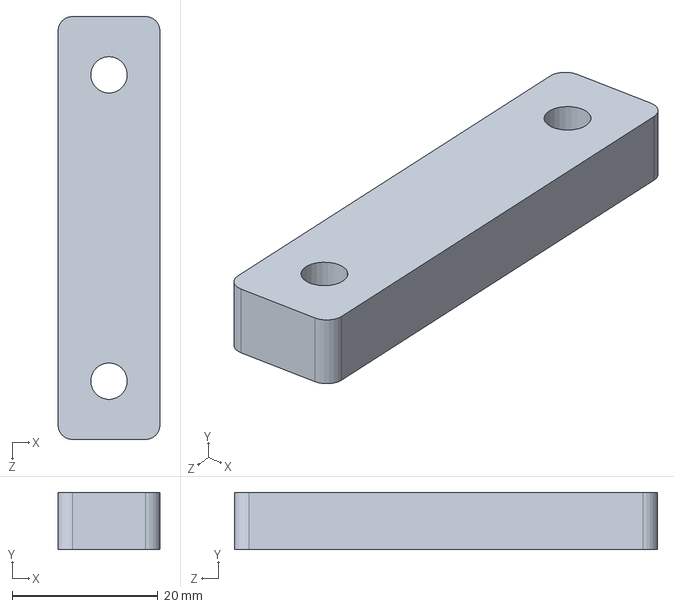
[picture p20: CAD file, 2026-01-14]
B - CAD/P2-5-2 Pillow Block Bearing Mount/P2-5-2 Pillow Block Bearing Mount.SLDPRT
14.0 x 7.83 x 58.0 mm

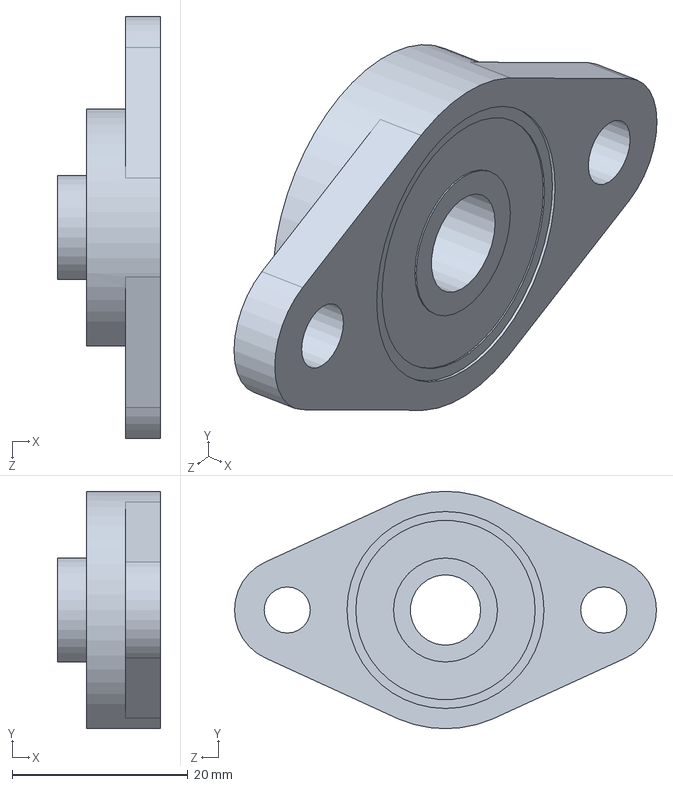
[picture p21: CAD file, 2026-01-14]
B - CAD/P2-9 Flange Bearing/P2-9 FlangeBearing.SLDPRT
11.7 x 27.0 x 48.0 mm

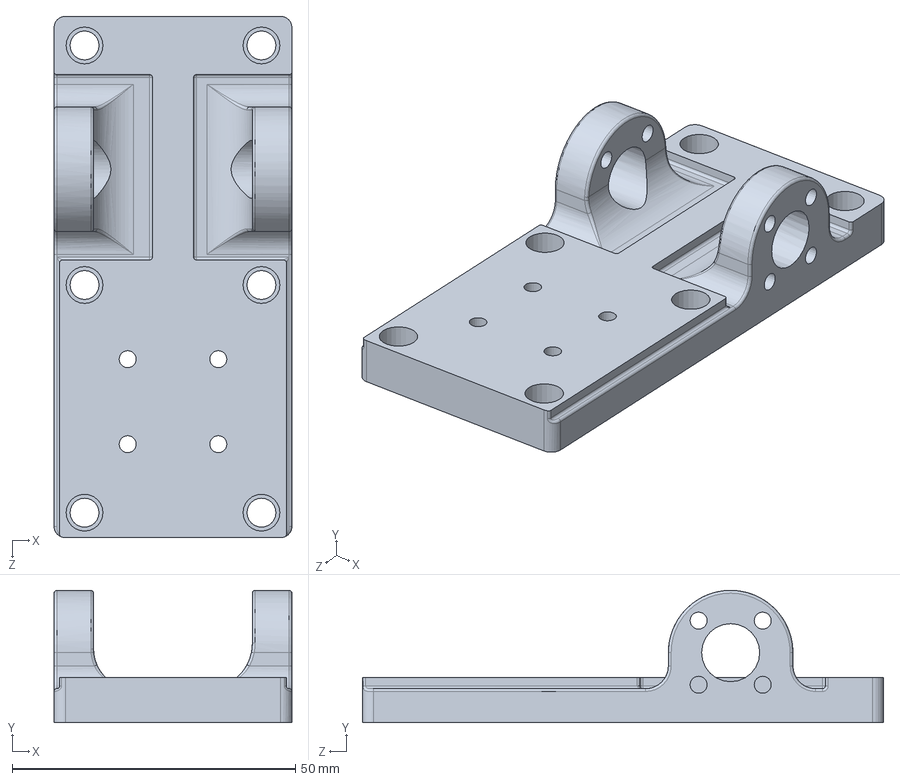
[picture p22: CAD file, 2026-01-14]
B - CAD/P3-1 Carriage/Carriage - 2025-11-09 - 2231.SLDPRT
42.0 x 23.4 x 92.0 mm

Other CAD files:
B - CAD/Full Assembly.SLDASM
B - CAD/P5-1 Arduino Due/P5-1 Due Assembly.SLDASM
B - CAD/P5-3-1 Driver Mnt and Mnt Asm/P5-3 ASM.SLDASM
B - CAD/Misc Test Pieces/M3 insert test.SLDPRT
B - CAD/Archive/608RS Bearing.SLDPRT
B - CAD/Misc Test Pieces/M5 insert test.3mf
B - CAD/Misc Test Pieces/M5 insert test.SLDPRT
B - CAD/Misc Test Pieces/M5 insert test.STL
B - CAD/P1-1 Chassis Body Print Asm/2025-11-10 - 855 - v0/P1-1 Chassis Body Print.3mf
B - CAD/P1-1 Chassis Body Print Asm/2025-11-10 - 855 - v0/P1-1-1 Chassis Body Print Flange End.SLDPRT
B - CAD/P1-1 Chassis Body Print Asm/2025-11-10 - 855 - v0/P1-1-1 Chassis Body Print Flange End.STL
B - CAD/P1-1 Chassis Body Print Asm/2025-11-10 - 855 - v0/P1-1-2 MotorEnd.STL
B - CAD/P2-1-2 MotorMount/MotorMount - 2025-11-09 - 1847.3mf
B - CAD/P2-1-2 MotorMount/MotorMount - 2025-11-09 - 1847.SLDPRT
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

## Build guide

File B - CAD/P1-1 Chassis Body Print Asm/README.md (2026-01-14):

# Part: P1-1 Chassis Body
This is the part of the mechanical assembly that everything bolts down to.

**As of 2026-01-13:** This is a 3D printed part, and I had to split it into two pieces since it didn't fit in my print area. There is too much dimensional error in the print. Having it in two pieces isn't ok, and having it made of plastic is probably not OK either. 

 The pieces that mount on this chassis need to be really well aligned, and stable in their positioning, so the chassis body needs to be a reliable source of 'dimensional truth' that all other parts can rely on. 
 
 In the future I should use a piece of T-Slot rail to do this job. Plastic changes its dimensions too much with temperature and humidity.

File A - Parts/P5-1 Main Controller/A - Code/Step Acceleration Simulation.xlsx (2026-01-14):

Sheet: Sheet1
 | Initial Velocity (mm/s) | 0 |  |  | steps represented as n
 | Acceleration (mm/s2) | 2 |  |  | Microsteps represented as un
 | Max Velocity (mm/s) | 25
 | Min Velocity (mm/s) | 0.01
 | FullStepsPerRev (n/rev) | 200
 | _microStepMultiplier (un/n) | 32 |  | IMPORTANT NOTICE
 | DispPerRevolution (mm/rev) | 8 |  | Note the case of decelerating from max speed. The rounding error keeps us STUCK at full speed since our time delta depends only on past velocity
 |  |  |  | and current acceleration. If we are going fast, then the rounding errors make these the same each time through the loop, and we don't ever make any
 | MmPerMicroStep(mm/un) | 0.00125 |  | progress slowing down. There would be a similar issue speeding up.
 | MicroStepsPerMm (un/mm) | 800 |  | To fix this, we need to keep an un-rouded accumulating time error. We determine the difference between our actual us period and our ideal calculated one, then add
 | InitialPos(un) | 0 |  | that to an error counter. Once the error counter counts up to 1 full us (positive or negative), we tack that on to our wait period, zero out the error counter, and continue.
 | InitialVelocity (un/s) | 0
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

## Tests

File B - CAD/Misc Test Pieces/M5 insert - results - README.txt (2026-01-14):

The 6.5mm hole ended up being my favorite. Too small a hole, and you get the excess plastic melt going in the hole at the bottom, forcing you to chase with a tap.

Note: The 4.95mm hole ended up printing smaller. I couldn't fit the M5 bolt in there. Should probably design the hole at 5mm exactly, even though the bolt is 4.85mm. That's the amount of shrinkage, I guess.

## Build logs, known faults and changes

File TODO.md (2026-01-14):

# To-Do List

## Mechanical
* [ ] Design and print the male DB9 plug with strain releif

## Electrical
* [ ] Install the male DB9 plug with strain releif, and update plug position
* [ ] Add a voltage regulator module to power the microcontroller from the motor voltage source
  * [ ] Find parts
  * [ ] Design/Draw the board if no good single part found
  * [ ] Make the board if no good single part found

## Software
* [ ] Change ISR code to fixed-time calculations rather than fixed-displacement calculations
* [ ] Implement a G-code interpreter
  * [ ] Create a function to chain movements together
  * [ ] Create a function to interpret g-code syntax into the chain planner

## Documentation
* [ ] Finish putting all the purchase links into document "3 - Parts.md"
* [ ] Add the power plug assembly to the parts list
* [ ] Add the male DB9 parts to the parts list
* [ ] Generate document "4 - Ports.md"
* [ ] Generate document "5 - Connections.md"
* [ ] Make a diagram for the electrical mounting
* [ ] Make an electrical schematic diagram for the control board

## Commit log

2026-01-14 initial upload
    [1 - Assembly Definition Document.xlsm, 608RS Bearing.SLDPRT, Carriage - 2025-11-09 - 2231.SLDPRT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]
2026-01-14 Updates to MD files including the README, Parts, TODO
    [Full Assembly.SLDASM]
